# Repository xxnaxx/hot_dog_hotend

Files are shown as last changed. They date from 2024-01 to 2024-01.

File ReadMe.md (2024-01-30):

# 热狗3D打印机热端（手搓版）

## 特点
```
使用两片陶瓷加热片，加热更均匀快速，外形酷似热狗，固名曰“热狗热端”
大部分配件都是可以购买的成品，手搓部分较少，并且设计了辅助手搓的打印件
喷嘴使用火山喷嘴，便宜且选择多
加热块长度比火山长40%，有效提高流量
```

### 流量测试结果
```
PLA:
杂牌白色
0.4喷嘴
喷头230°C
最大流量：56mm³/s

PETG:
兰博黄色
0.4喷嘴
喷头270°C
最大流量：42mm³/s

ABS:
K家草绿
0.4喷嘴
喷头280°C
最大流量：48mm³/s
```

### 1# 加热块手搓方法
用打印件，将螺柱、304不锈钢螺母、M6螺丝固定起来，如下图，然后用锉刀打磨出所需要的凹槽，因为铝比不锈钢软很多，不锈钢螺母起到“定位”的作用，不会搓过头
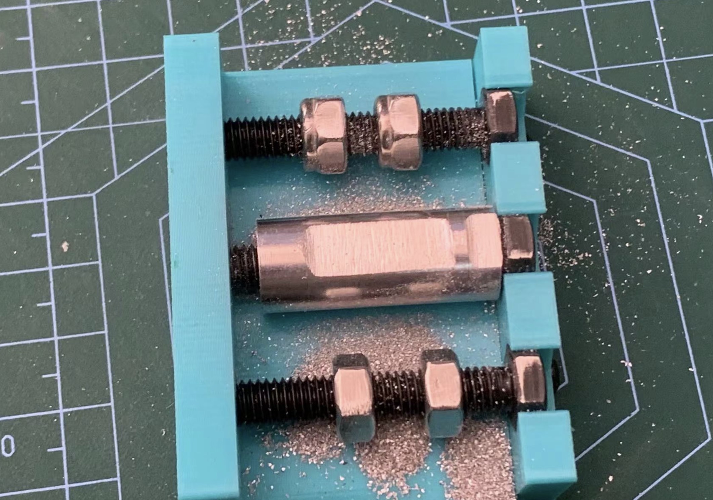
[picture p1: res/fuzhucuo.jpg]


### 2# 陶瓷加热片与加热块的固定方式
加热片与热端之间涂上导热硅脂，然后用电热丝缠绕绕颈，缠绕的方式可以参考钓鱼佬缠鱼钩的方式，咨询搜索视频。成品如下图：
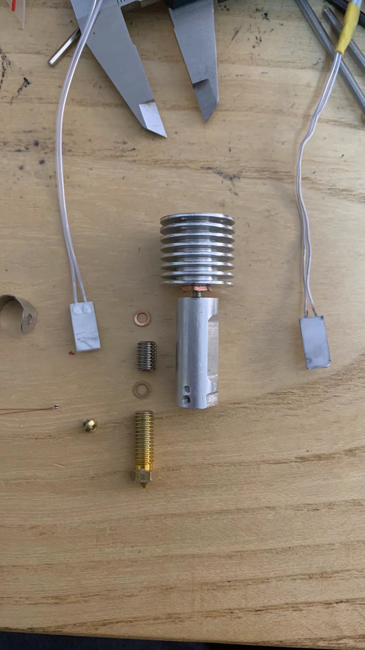
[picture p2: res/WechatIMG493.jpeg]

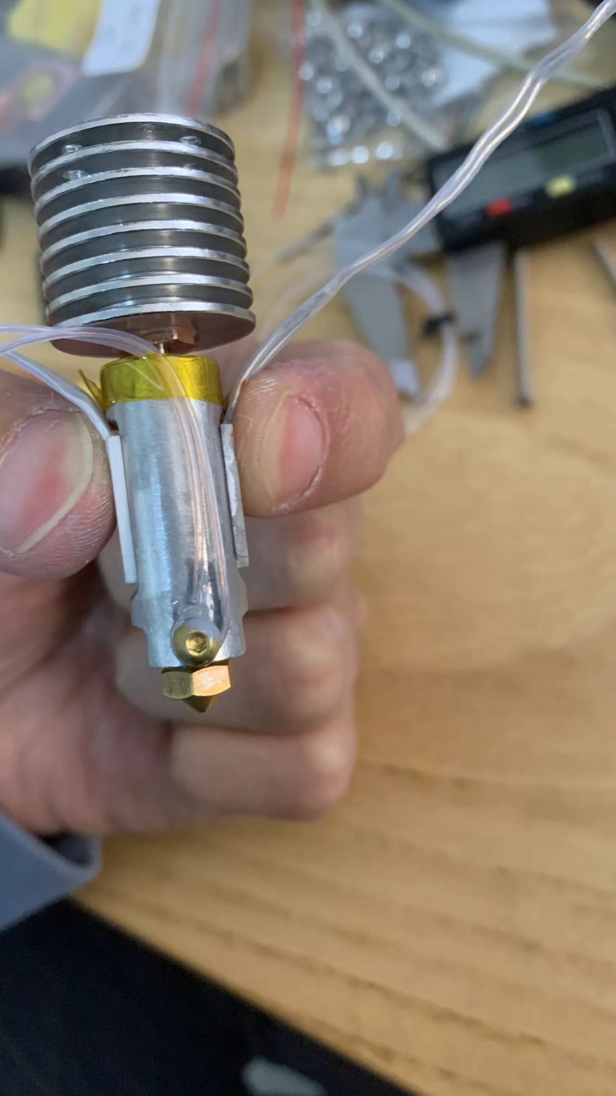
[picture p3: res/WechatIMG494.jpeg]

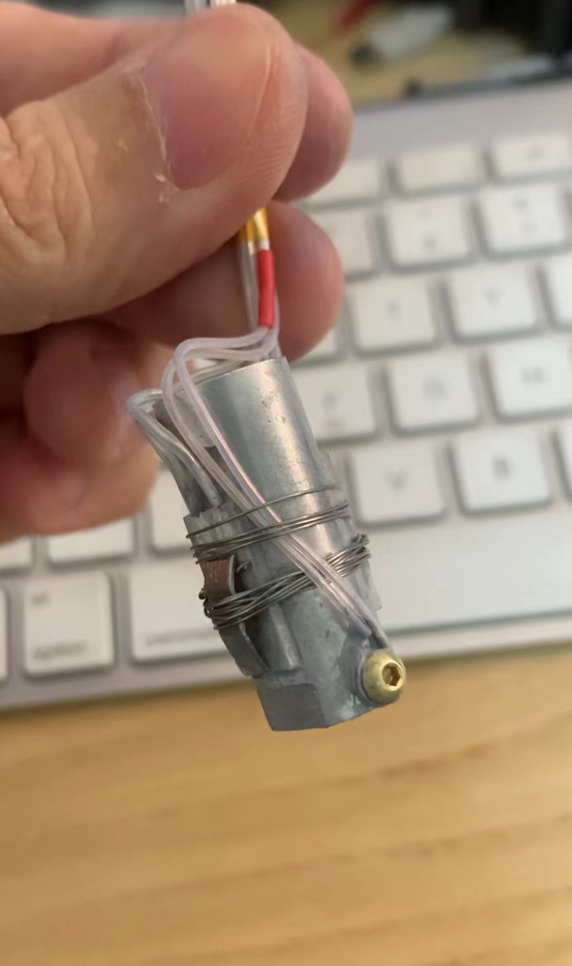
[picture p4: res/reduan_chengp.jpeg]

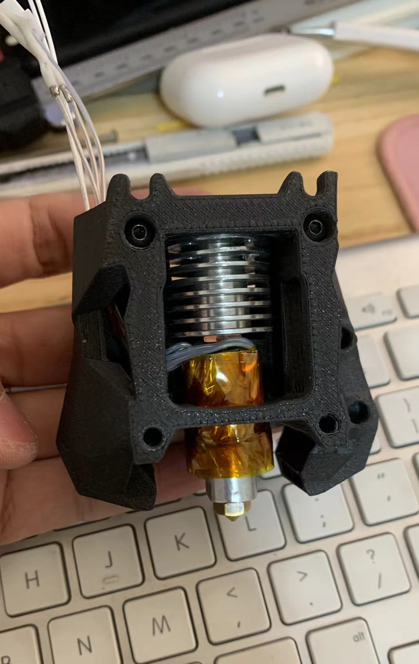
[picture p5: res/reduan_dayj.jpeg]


### 3# 所需工具
台钻或手电钻、1.5mm钻头、M2.5丝锥、6寸钢锯锯片

**注：以下购买链接只是方便群友购买，与本人没有利益关系，有问题找客服

### 陶瓷加热片
数量：2片
备注：24v/45瓦的已经足够，当然也可以买80W的，要考虑自己的主板或者CAN板能不能受得了（当然，Klipper可以调节功率，可查阅文档）
【淘宝】https://m.tb.cn/h.5IOO5F6JRaUB51y?tk=rVt8W8G8Dlu
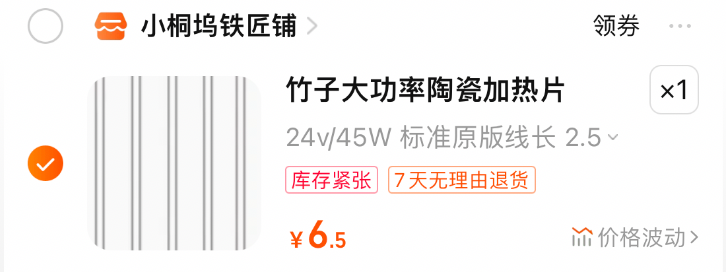
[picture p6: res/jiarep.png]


### 热敏
用竹头的热敏或者V6的波封热敏即可

### 铝合金螺柱
数量：n
备注：这个店的螺柱似乎是分别从两端攻丝的，所以并不是“通孔”，而我们需要的是通孔的，可以用M6的螺丝强行通，我买过3个，有两个是可以通的，所以建议多买几个，或者找找其他店
【淘宝】https://m.tb.cn/h.5sTuuAdTqyv3Jh5?tk=3x9uW8GJLnA
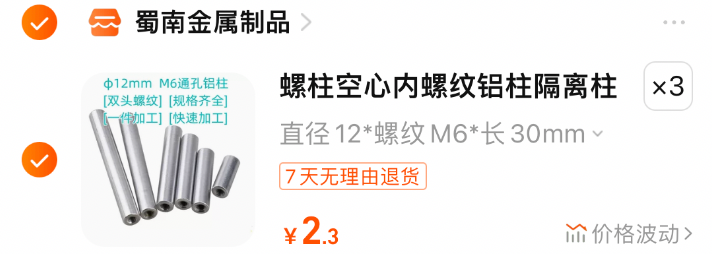
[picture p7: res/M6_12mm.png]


### V6散热片
数量：1
备注： 买远端V6，需要锯头并钻孔，保留8片散热鳍片即可。辅助工具在stl文件夹
【淘宝】https://m.tb.cn/h.5IOpfrfORYHuSAF?tk=5FU2W8GN9Y9
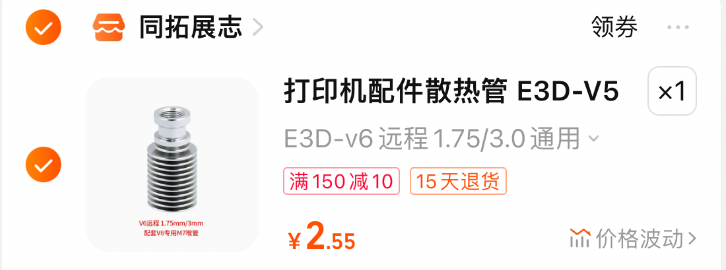
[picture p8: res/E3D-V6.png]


### 喉管
数量：1
备注：这种双金属喉管可以打高温（大概300°C），并且不容易堵头，不过缺点是容易断，也可以换其他喉管
【淘宝】https://m.tb.cn/h.5IZALrTk8m8hj00?tk=fgMAW8GMsE5
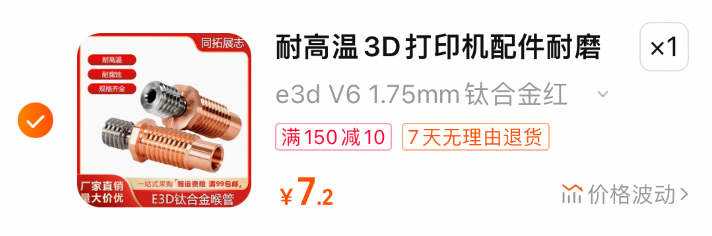
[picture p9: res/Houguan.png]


### V6喷嘴过渡块（延长块）
数量：1
备注：用来延迟火山喷嘴，以便于可以适配30mm的加热块
【淘宝】https://m.tb.cn/h.5rQBDU31OXDRRmV?tk=cz6sW8GpYWz
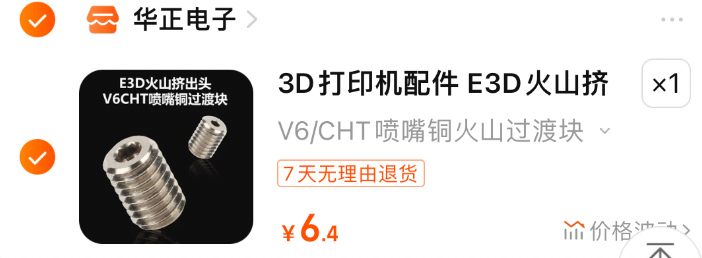
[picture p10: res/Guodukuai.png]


### 紫铜垫片
数量：2
备注：防止漏料用
【淘宝】https://m.tb.cn/h.5I0cyUBQvIiHrqF?tk=7JFIW8GrOHc
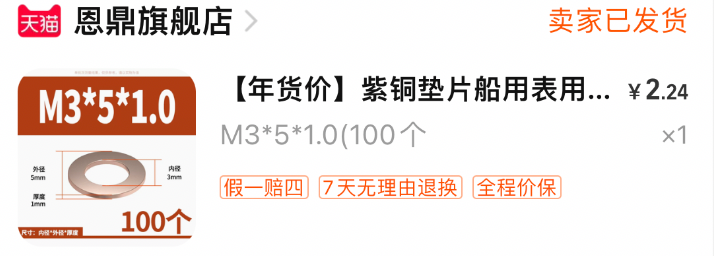
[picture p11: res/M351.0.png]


### 螺丝螺母
M2.5*3用于固定热敏
M2.5*8用于将V6散热器固定到打印头上
M6螺丝用于辅助搓热端铝块
M6螺母也用于辅助搓热端铝块
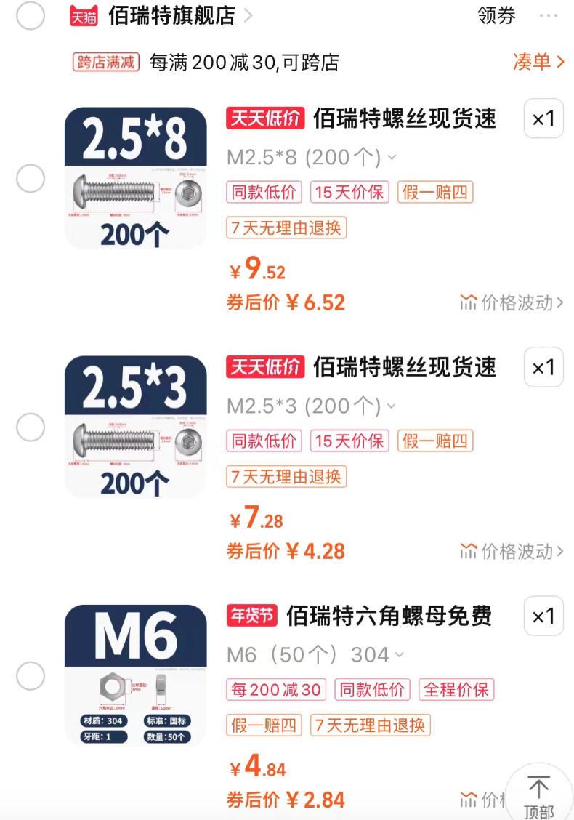
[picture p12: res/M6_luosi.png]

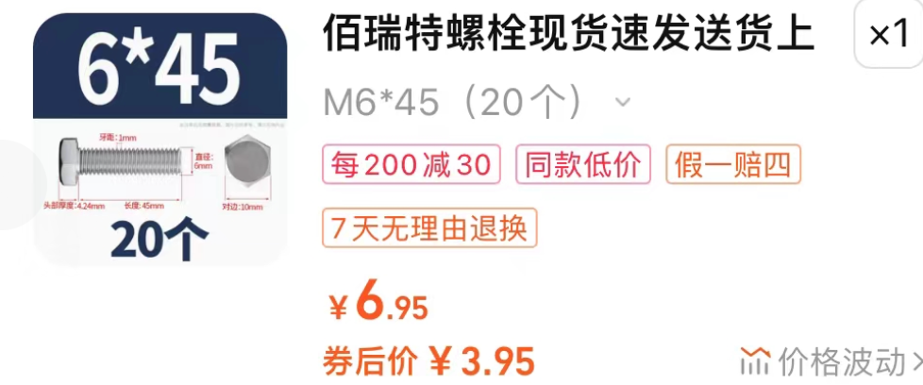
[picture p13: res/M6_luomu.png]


## 工具
### 钢锯锯片
备注：只需要买锯片即可，锯片手柄可以用打印件，模型在stl文件夹
【淘宝】https://m.tb.cn/h.5ImjHXCLdrumGd5?tk=pSKjW8uib15 
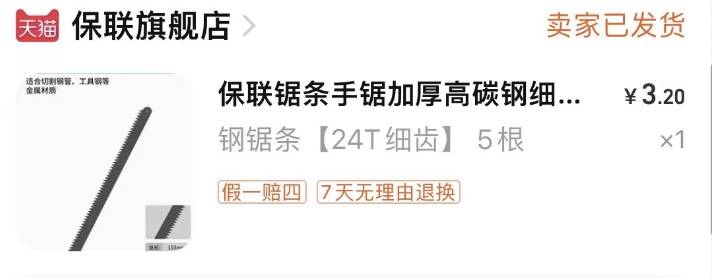
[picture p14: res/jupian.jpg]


### 若有任何问题可加Q群：826045677  @John
### 注：请勿商用！！！

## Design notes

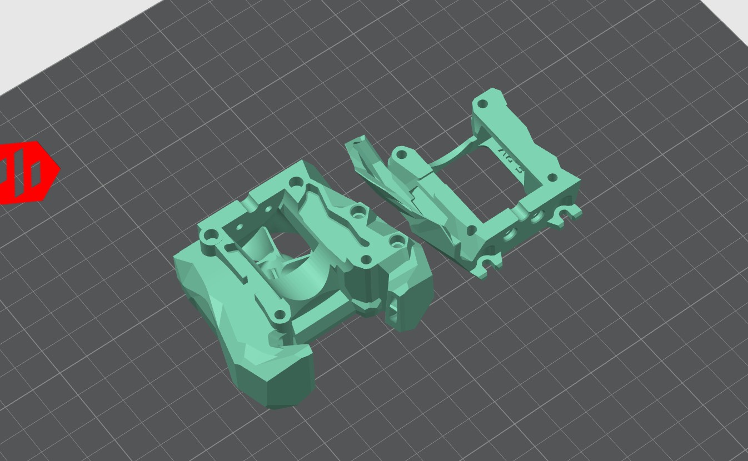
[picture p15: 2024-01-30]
stl/热狗-SB热端.jpg

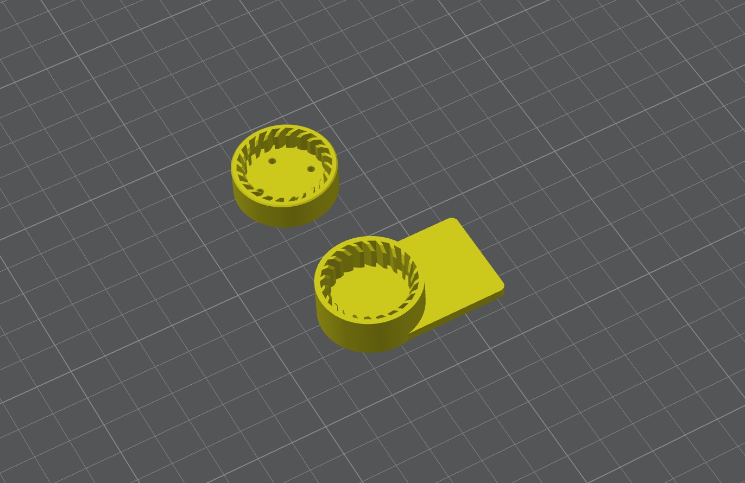
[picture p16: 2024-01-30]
stl/V6打孔辅助.jpg

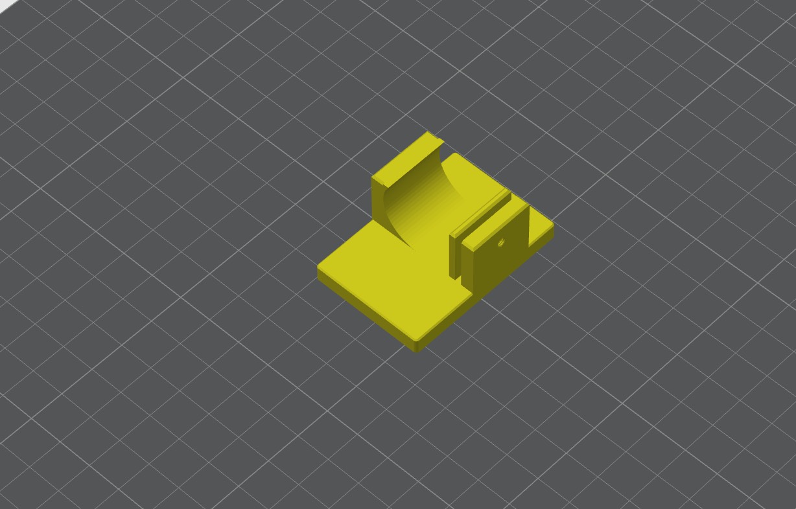
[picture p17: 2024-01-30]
stl/V6锯头固定件.jpg

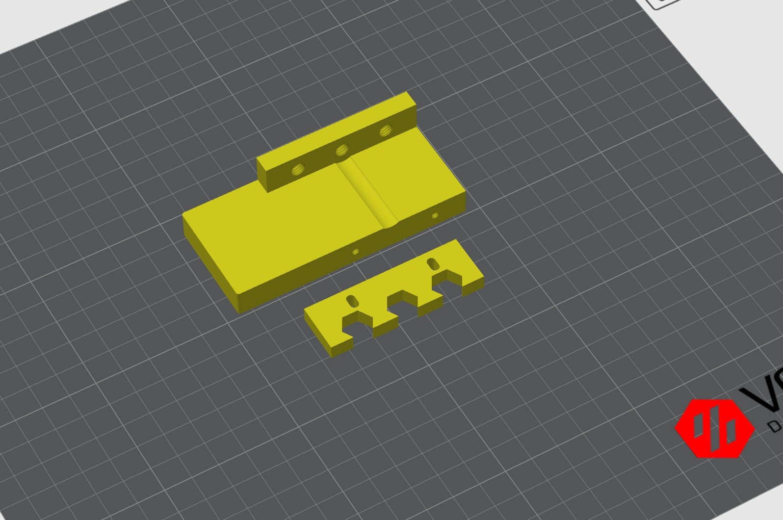
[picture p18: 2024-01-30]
stl/搓加热块辅助.jpg

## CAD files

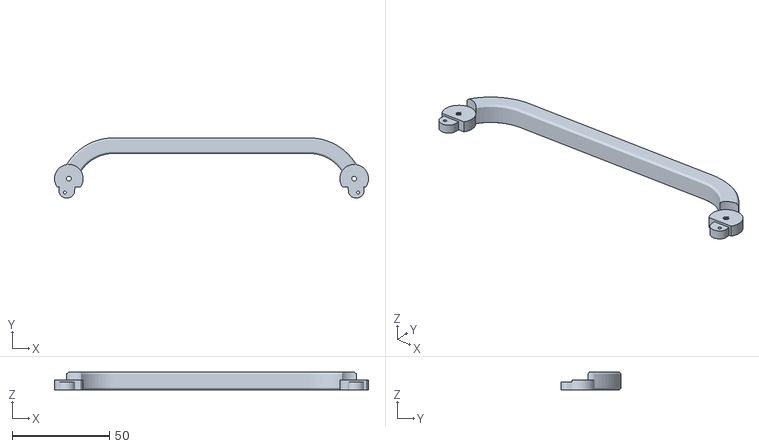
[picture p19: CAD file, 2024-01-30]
stl/6寸钢锯句柄-主体.stl
161.1 x 30.9 x 9.00

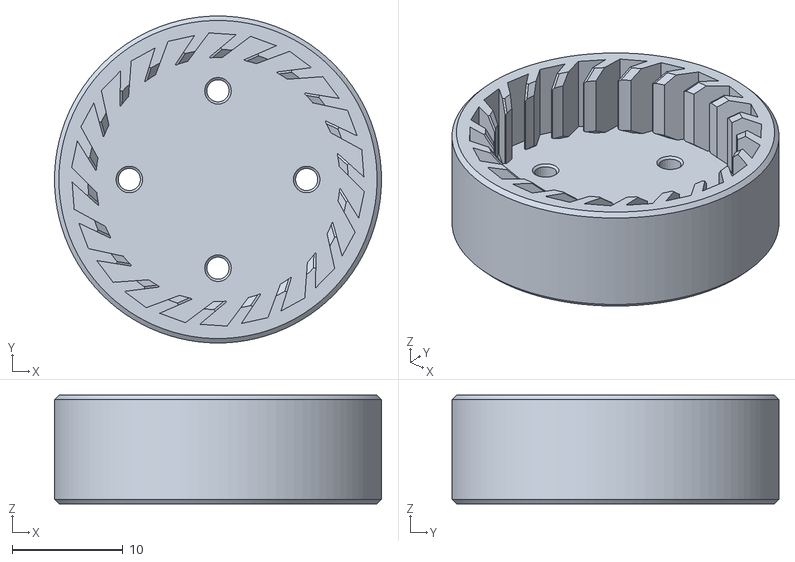
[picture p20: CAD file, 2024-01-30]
stl/V6打孔定位件.stl
29.5 x 29.5 x 9.80

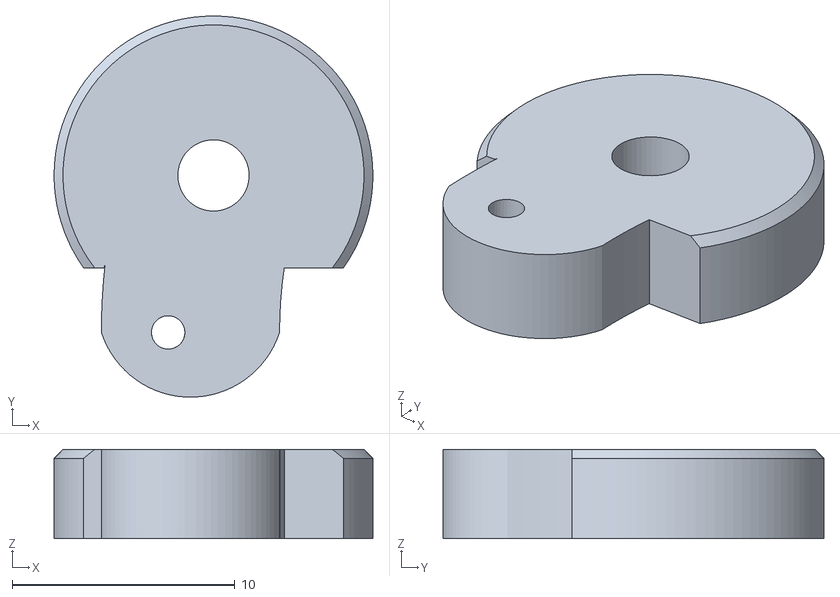
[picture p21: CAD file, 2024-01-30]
stl/6寸钢锯句柄-固定L.stl
14.3 x 17.1 x 4.00

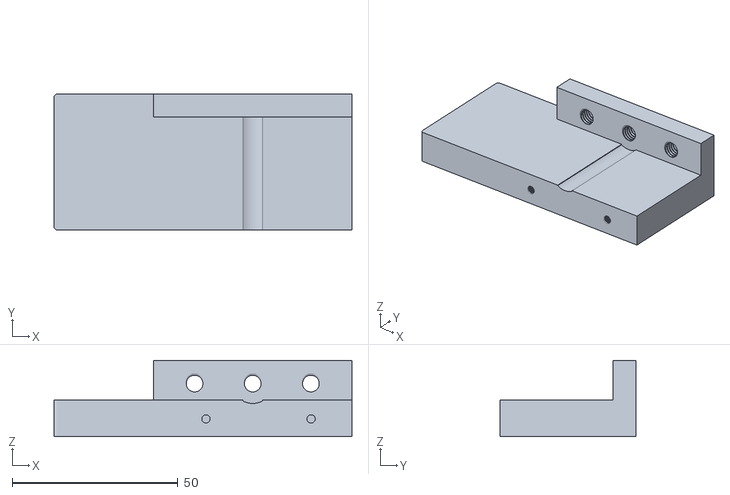
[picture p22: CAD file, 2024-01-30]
stl/搓加热块辅助1.stl
89.9 x 41.0 x 22.9

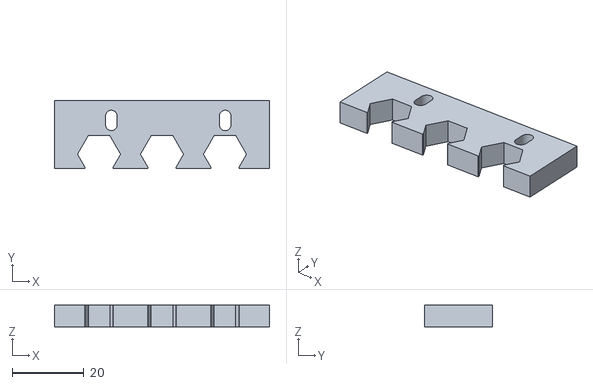
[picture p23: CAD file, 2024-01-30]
stl/搓加热块辅助2.stl
59.9 x 18.9 x 6.00

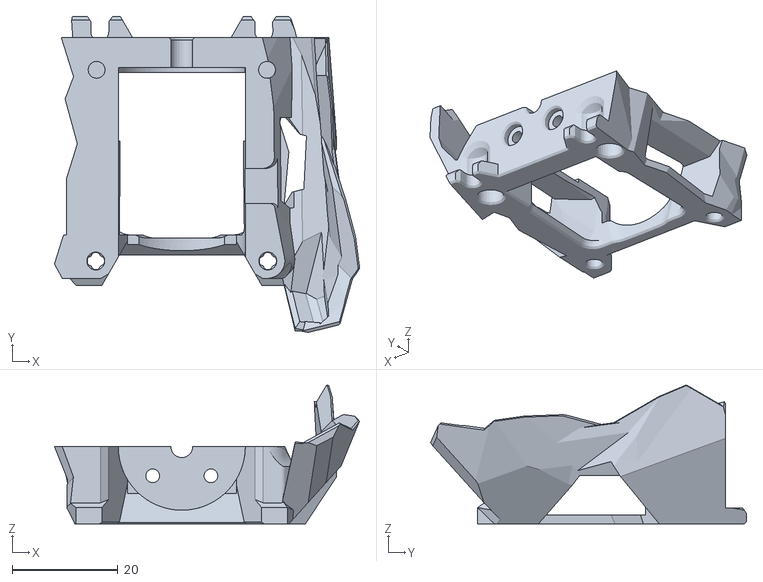
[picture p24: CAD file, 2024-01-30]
stl/热狗-SB热端B.stl
57.7 x 59.7 x 26.3

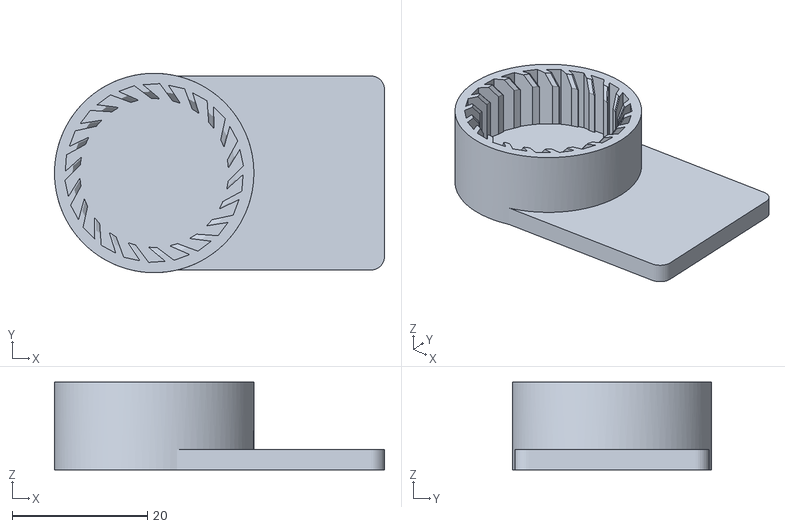
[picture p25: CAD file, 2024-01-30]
stl/V6固定座.stl
48.8 x 29.5 x 13.0

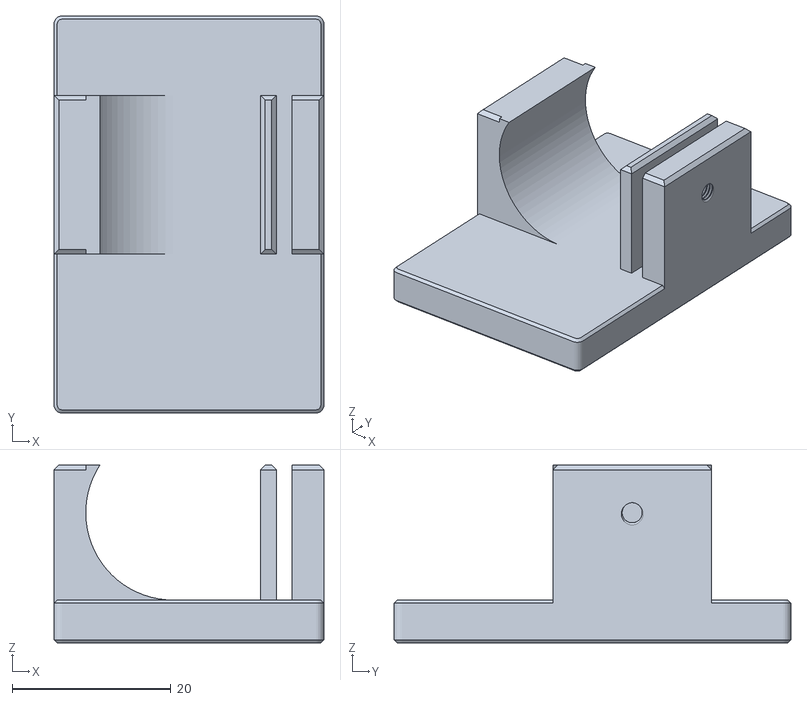
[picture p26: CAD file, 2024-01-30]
stl/V6锯头固定件.stl
34.0 x 50.0 x 22.4

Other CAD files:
stl/6寸钢锯句柄-固定R.stl
